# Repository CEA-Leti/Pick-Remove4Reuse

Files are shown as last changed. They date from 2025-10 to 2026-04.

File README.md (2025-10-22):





**Pick&Remove4Reuse**
---------------------
Système de récupération de composants électoniques automatisé basé sur une imprimante 3D open source Creality Ender3.

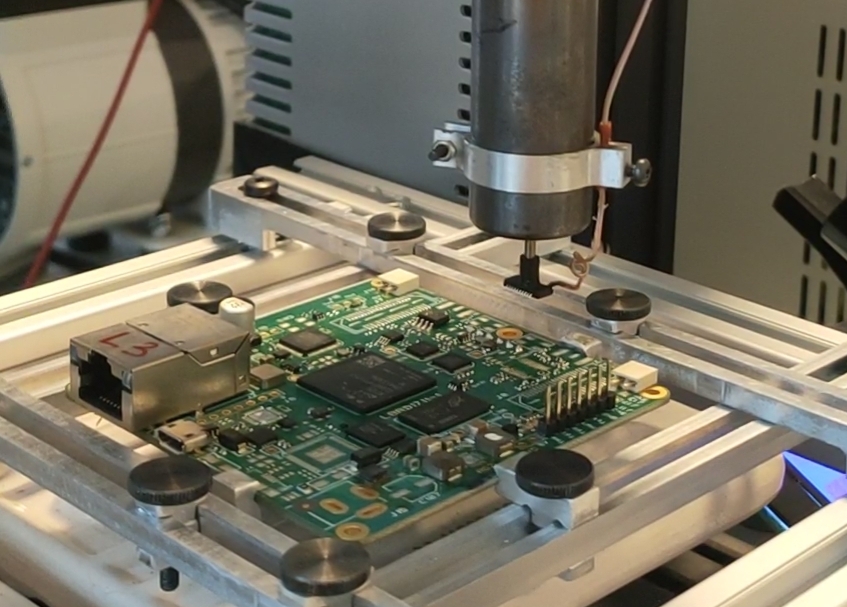
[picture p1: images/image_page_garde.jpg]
Récupération composants

## Introduction

Ce document a pour objectif de recenser le travail effectué lors de mon stage de fin d'étude qui avait pour objectif de concevoir un système automatisé de récupération de composants électroniques (ECs). Ce domument a également pour objectif d'assister tuote personne qui souhaiteraient reproduire ou reprendre ces travaux.
Mon rapport de stage, détaillant le travail effectué se trouve à l'adresse suivante :
> "doc/Rapport_PFE_Margaux_Anne_CEA_INSA.pdf"

Lors de mon stage, j'ai pu concevoir, fabriquer et tester une station de récupération automatisée de composants électroniques en vue de leur réemploi. Les résultats sont prometteurs. La station permet une récupération de composants CMS d'une taille pouvant varier en fonction de la taille de la buse. L'impact CO2 en termes d'énergie utilisée lors de la récupération s'est révélé inférieur à celui de la fabrication. Le temps nominal de récupération d'un composant électronique est de 1'30 et peut prendre jusqu'à 2'30.

## Prise en main rapide de la station une fois mise en place
*   Positionner la carte sur le support de carte. Il est nécessaire de dévisser uniquement les vis moletées se trouvant sur le bras de gauche et du haut. Attention, les bords de la carte doivent être alignés sur le support de carte. Le coin inférieur gauche de la carte une fois positionné doit correspondre au coin auquel les composants sont référencés dans le fichier de fabrication.
*   Vérifier que la ventouse du pistolet corresponde à la taille des ECs visé pour la récupération
*   Allumer la plaque IR pour préchauffe de la carte (15 min mini)
*   Brancher la carte Arduino et l'imprimante à l'ordinateur
*   Ouvrir le script python avec Spyder
> "src\Test_imprimante_positionement.py"
*   Utiliser python 3.10  (clique-droit sur la console>New console in environment>Custom: Python310)
*   Un fichier de config permet de configurer certains paramètres, on retrouve par exemple la hauteur de sécurité afin d'éviter que le pistolet ne percute des éléments de la structure ou de la carte. On retrouve également la hauteur delta permettant le chargement du ressort, permettant le désassemblage, cette hauteur peut être modulée en fonction du positionnement du capteur de fin de course et du chargement que l'on souhaite effectuer sur le ressort. Des valeurs prédéfinies sont rentrées, il est possible de les modifier au besoin.
> "src\config.ini"
*   Allumer l'imprimante et la station Hakko
*   Lancer le programme : ce dernier va commencer par initialiser l'imprimante. Il vous demandera ensuite de fournir un fichier Excel avec la position des ECs à récupérer. Un exemple de fichier se trouve au chemin ci-dessous. Une fois le fichier fournis, il vous sera demandé de référencer le premier composant à récupérer du fichier Excel. Pour ce faire, vous pouvez vous déplacer avec la molette de l'imprimante en suivant les instructions fournie par le programme. Une fois la position validée, la récupération débute. Des messages d'information sont visibles sur l'imprimante afin de vous tenir au courant sur l'avancée de la récupération.
> "src\composants_recup.xlsx"
*   Si vous voulez interrompre la récupération, faites 'ctrl C' dans la console. Il vous sera ensuite nécessaire de débrancher et de rebrancher la carte Arduino afin de relancer le programme sans erreurs.
*   Un mode d'emploi présente les explications ci-dessus en annexe du rapport de stage.

## État de l'art
Mon stage a débuté avec l'établissement d'un état de l'art qui recense un certain nombre d'articles scientifique sur les Déchets d'Équipements Électriques et Électroniques (DEEE), le recyclage des cartes et ECs, ainsi que sur la récupération des ECs en étayant également les perspectives en termes de conception alternative afin de faciliter la récupération, la réutilisation et le recyclage des systèmes électroniques.
Le document se trouve ici:
> "doc\Rapport_bibliographique_recuperation_EC.pdf"

## Choix des outils fonctionnels
L'essentiel des outils, dispositifs, achats effectuées au cours du stage sont recensées sur:

> "documentation\Materiel.xlsx"

## Conception
Après avoir fait les différents choix fonctionnels ainsi que choisi les briques fonctionnelles, la conception des différents éléments d'intégration a débuté.
Le fichier ci-dessous contient les différents sous-fichiers correspondants aux éléments de conception. 
> "solidworks"

La CAO du système général avec tous les éléments assemblés se trouve ici:
> "solidworks\support_carte_asm_g\asm_general_v3.SLDASM"

## Commande et mesure station Hakko
Afin de commander et d'avoir un retour de la station Hakko (commande du pistolet permettant le dessoudage et le désassemblage), il a été nécessaire d'ouvrir cette dernière.
Pour ce faire, il est nécessaire de dévisser les quatre vis fixant le cadre de la face avant de la station ainsi que les deux vis se trouvant sur la face arrière de cette dernière. Le cadre du bas tient alors encore en place grâce à un clip se trouvant sur la face du bas de la station accrochant le cadre avant et le carter de la station. Une fois déclipsée, il est  ainsi possible d'ouvrir la station. L'image ci-dessous illustre nos deux points d'intérêt. À savoir, le bouton permettant l'actionnement du cycle et le buzzer donnant des informations sur l'état du cycle.

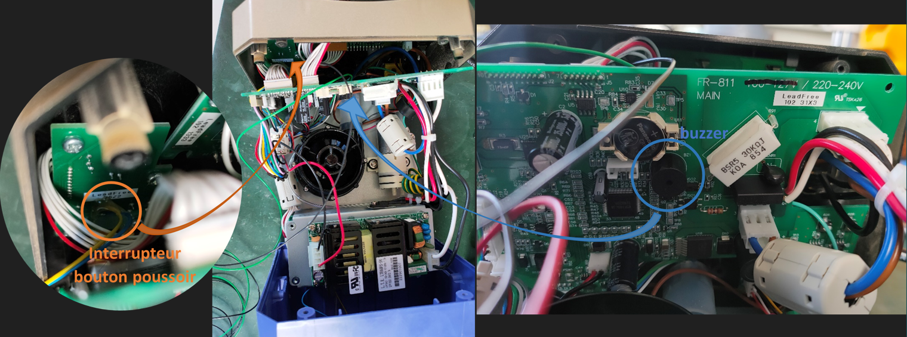
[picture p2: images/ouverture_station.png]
hghg Ouverture station Hakko


Il est alors nécessaire de souder des fils sur les bornes de l'interrupteur et celles du buzzer.

* Une fois ceci fait, les deux fils de l'interrupteur sont soudés sur un relai 5 V. L'objectif avec l'utilisation du relai est qu'il agisse comme un interrupteur commandé. Selon le signal de commande envoyé par la carte Arduino au relai, celui-ci effectue une connexion ou non entre les deux fils soudés aux bornes du bouton de la station, déclenchant/stoppant ou non le cycle de chauffe. Le fil soudé sur la commande du relai est branché sur un pin analog de la carte Arduino. Le second fil est lui relié au 5 V de l'Arduino. Une diode est également soudée entre les deux pins (commande/puissance) du relai.

* Les fils du buzzer sont eux fixés sur les pins de la carte Arduino. L'un des fils doit être relié à la masse, quant à l'autre à un pin digital (PWM) de l'Arduino. Lors du soudage des fils, celui devant être relié à la masse doit être vérifié. Pour cela, testez avec un multimètre quelle borne du buzzer y est connectée en vous aidant de la pile (se trouvant à côté de ce dernier sur la carte de la station) qui a elle-même une borne reliée à la masse.

## Intégration du capteur de fin de course:
Le capteur de fin de course est relié à la carte Arduino. Ce dernier possède 3 bornes. Une étude de la datasheet vous permettra de comprendre son fonctionnement. Dans la pratique, l'une des bornes sera reliée à l'alimentation de la carte (3,5 V par exemple) et l'autre à un pin digital de l'Arduino. Pour le bon fonctionnement, une résistance de pull down est également nécessaire pour cette même sortie.

## Commande - Script Python
En parallèle de la conception des différents éléments d'intégration, la commande du système a été conçue. Cette dernière est assurée par un script Python se trouvant ici :
> "src\PickRemove.py"

Ce dernier est associé à un fichier de configuration généré par un script Python permettant la modification de certains paramètres. Le réglage des paramètres est détaillé par la suite.

Afin que le script fonctionne, plusieurs choses sont nécessaires:

* Connexion en port série avec l'imprimante 3D : connecter l'imprimante et l'ordinateur en vérifiant que le numéro du COM série pré-rentré dans le fichier de configuration est le bon (vérifier à l'aide du gestionnaire de périphérique de votre ordinateur)

* Connexion à la carte Arduino permettant le contrôle du cycle de chauffe, la mesure de l'étape de ce dernier ainsi que l'état du capteur de fin de course. Connecter en port série la carte Arduino et l'ordinateur. Comme pour l'imprimante 3D, il est nécessaire de vérifier le numéro du COM série pré-rentré dans le fichier de configuration. 
Afin de configurer la carte Arduino lors de la première utilisation, un programme doit lui être transféré, permettant d'utiliser la librairie PyFirmata utilisée dans le script Python. Il est alors nécessaire de se rendre dans l'IDE Arduino 
`Fichier>Exemples>Firmata>StandarFirmata`

* Installer les différentes librairies :

    * Pour installer la bibliothèque pyFirmata il faut taper la commande suivante dans la console Python : `!pip install pyfirmata`

* Installation de la version `Python 3.10` afin d'utiliser la librairie pyFirmata. Une fois l'installation effectuer, il faudra dans la console Python générer une nouvelle console avec la version 3.10 (clique-droit sur la console>New console in environment>Custom: Python310).

## Réglage script Python
Les différents paramètre modifiable, pour le réglage du système de récupération, sont regroupés dans un fichier de configuration modifiable :

> "src\config.ini"

> "src\Creation_fichier_config.py"

Celui-ci permet de définir certains paramètre expliqué ci-dessous :
[DEFAULT]
* portImprimante = COM7
* portArduino = COM5
* baudrate = 115200 : vitesse de discussion entre le script Python et l'Arduino
* pin_finDeCourse = 7
* pin_buzzer = 2
* pin_relaiCycleChauffe = 4

[Constante]
* vitesse_deplacement = 3000 : définition de la vitesse de déplacement de l'imprimante

* pos_x_min_depose_ec = 96 : définition de la position en x du premier emplacement de dépose d'EC.
* pos_x_max_depose_ec = 229 : définition de la position en x du dernier emplacement de dépose d'EC.
* espacement_ec_depose_x = 19 : Espacement en x entre deux positions de dépose.
* pos_y_min_depose_ec = 35 : définition de la position en y du premier emplacement de dépose d'EC.
* pos_y_max_depose_ec = 38.8 : définition de la position en y du dernier emplacement de dépose d'EC.
* espacement_ec_depose_y = 0.4 : Espacement en y entre deux positions de dépose.
* hauteur_secu_z = 35 : hauteur de sécurité afin de ne pas percuter des éléments avec le pistolet lors de ses déplacements en x et y.
* delta_z_posDesassemblage = 4 : distance delta nécessaire pour venir charger le ressort lors du désassemblage.

## Initialisation station Hakko
Initialisation du cycle de chauffe dans la station Hakko. Le cycle de chauffe prédéfini à charger sur la station se trouve ici:
>"src\Hakko\cycle_chauffe_hakko.csv"

Trois options s'offrent à vous :
* Réglage manuel directement sur la station
* Import du cycle via une clé USB
* Import du cycle via le port série de l'ordinateur (nécessite l'installation d'un pilote sur l'ordinateur). La démarche à suivre est décrite dans le manuel d'utilisation de la station.

La courbe de température à suivre est détaillée dans le fichier OneNote ci-dessous :
>"doc\Température dessoudage.one"

## Modification Imprimante 3D
*   **Modification des branchements de la carte**:
La carte de l'imprimante 3D se trouvant sous le plateau de cette dernière (cf image ci-dessous) permet de commander l'imprimante en position avec la commande de trois moteurs pas à pas (un pour chaque axe). Afin de faire le 0 de l'imprimante, la présence de capteurs de fin de course est également nécessaire. Nous retrouvons aussi un ventilateur permettant de prévenir la carte d'une potentielle surchauffe. La carte est par ailleurs alimentée, nous retrouvons ainsi deux fils branchés sur un bornier dans le but d'assurer cette fonction.
Outre ces fonctions, on retrouve aussi des éléments propres à l'impression 3D : alimentation de la chauffe de la buse (bornier 3 sur l'image ci-dessous) et du plateau (2), ventilateur lié à la buse (1), thermistance afin de mesurer la température de la buse et du plateau et permettre leur régulation respective. Ces derniers éléments ne nous sont plus nécessaires, ainsi, nous pouvons les enlever pour ne garder que l'utile de l'imprimante. Attention, il n'est néanmoins pas possible de retirer les thermistances. En effet, une fois débranchée, la température mesurée est erronée, ce qui engendre une erreur de l'imprimante. Ainsi, nous pouvons uniquement retirer les éléments branchés aux trois borniers latéraux gauches (1,2 et 3) ainsi que la commande du moteur d'approvisionnement en filament. Le premier bornier, initialement prévu pour l'alimentation du ventilateur associé à la buse d'impression, fournit une tension de 24V en continu. Ainsi, nous pouvons nous en servir afin de brancher un régulateur en température si besoin est de réguler la plaque IR. Dans mon cas d'étude, la plaque IR était alimentée à 60V, avec un générateur de puissance, ce qui ne permettait pas d'atteindre une température de préchauffe de la carte supérieure à 130°C. Ainsi, il n'a finalement pas été nécessaire de la réguler en température, étant donné que le seuil de préchauffe à ne pas dépasser est beaucoup plus haut (150-200°C). S'il vous est nécessaire de réguler en température la plaque, il est alors possible d'utiliser un régulateur de température, en fonction de la tension de commande max de l'outil en question, vous aurez peut-être besoin de réguler la tension sortant du bornier avec un régulateur 24V --> 5V par exemple. La puissance peut elle provenir directement du générateur 60V dans le cas où votre régulateur est isolé entre la commande et la puissance.
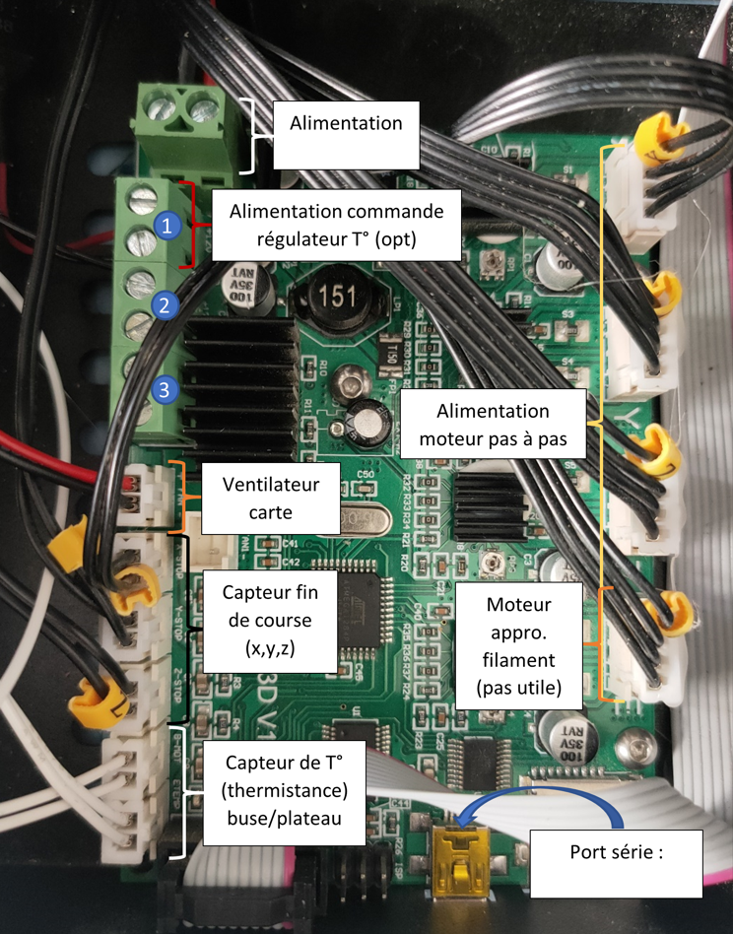
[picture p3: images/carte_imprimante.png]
hghg Carte imprimante 3D


*   **Modification sur la structure de l'imprimante:**
    * Afin de limiter le poids se trouvant sur la structure de l'imprimante se déplaçant selon z, vous pouvez démonter le moteur pas à pas initialement prévu pour l'approvisionnement en filament.
    
    * Afin de limiter la course de l'imprimante selon z et ainsi empêcher la collision du pistolet avec la structure de l'imprimante, il est conseiller de déplacer le capteur de fin de course de l'axe z vers le haut (il est possible qu'il soit nécessaire de rallonger les fils reliant ce dernier à la carte de l'imprimante présenté en amont)

    * La tête d'impression tout comme la plaque chauffante doivent être démonté. Le pistolet sera intégré directement sur le support de la tête d'impression (comme illustré dans la CAO générale du système introduite en amont). Le support de carte sera lui monté directement sur le support de la plaque chauffante, tout comme le support de la plaque IR.

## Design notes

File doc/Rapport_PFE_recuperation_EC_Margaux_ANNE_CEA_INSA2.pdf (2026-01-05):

Margaux ANNE
Année universitaire 2024–2025

### Spécialité Mécatronique - Parcours P4 Master Imagerie, Robotique et Ingénierie pour le Vivant (IRIV)

Projet de fin d’étude MIQ5 - Mémoire de stage de Master 2

# Développement d’un système automatisé de récupération de composants électroniques en vue de leur réemploi

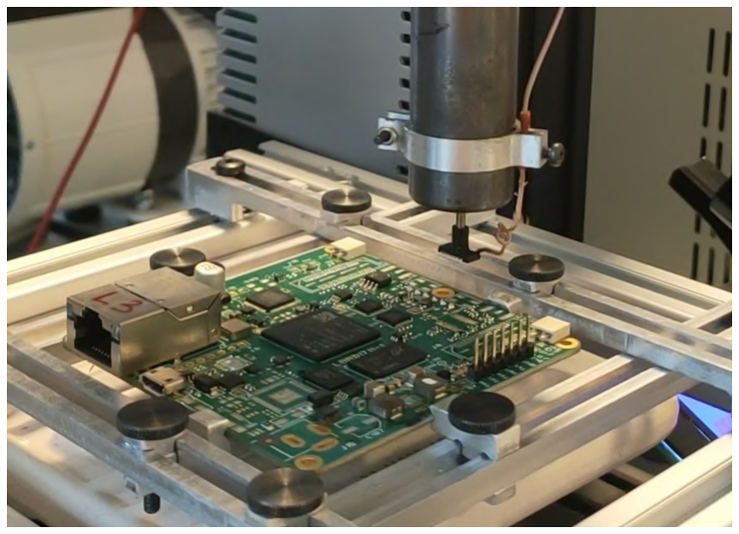
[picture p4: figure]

Organisme d’accueil :
CEA Grenoble
Encadrant : Sébastien BRULAIS
Adresse : 17 Av. des Martyrs, 38000 Grenoble Courriel : sebastien.brulais@cea.fr

Dates du stage : du 03/03/2025 au 21/03/2025 et du 07/04/2025 au 03/09/2025

## Résumés

### Résumé

Face au défi croissant posé par les déchets d’équipements électriques et électroniques (DEEE), un système automatisé a été développé pour récupérer des composants électroniques (EC) destinés à une réutilisation directe dans une logique de « seconde vie ». Ce projet répond à l’urgence d’agir contre l’augmentation des DEEE, qui représentent un risque majeur pour l’environnement et la santé. Avec l’accélération des avancées technologiques et la réduction de la durée de vie des appareils, la quantité mondiale de DEEE devrait atteindre 82 millions de tonnes d’ici 2030 [7]. Les méthodes classiques de gestion, comme la mise en décharge ou l’incinération, ne sont plus viables et engendrent des impacts environnementaux négatifs. Il devient donc essentiel de développer des solutions innovantes de recyclage et de réutilisation des ECs dans une logique d’économie circulaire [34]. Alors que certaines initiatives visent à extraire en masse des matériaux rares via des procédés chimiques (Ta, Ti, Ag, Au, . . .) [3], l’approche proposée cherche à récupérer des ECs à forte valeur ajoutée pour une réutilisation directe.
Un état de l’art a permis d’identifier les ECs présentant un fort intérêt économique et environnemental, ainsi que les méthodes adaptées à leur récupération sécurisée. Sur cette base, un outil de type « pick and remove » a été conçu. Sa structure repose sur le châssis d’une imprimante 3D Ender3 modifiée. Le préchauffage est assuré par un chauffage infrarouge (jusqu’à 150 °C), tandis qu’un pistolet muni d’une buse à air chaud (jusqu’à 260 °C) et d’un système d’aspiration assure le dessoudage localisé et le retrait des composants. Un script Python pilote la tête de l’imprimante, sur laquelle le pistolet est fixé, afin d’automatiser la récupération sur de petites séries de cartes.
Les premiers essais ont confirmé la faisabilité et l’efficacité du système, tout en apportant une première évaluation de ses bénéfices potentiels, tant économiques qu’environnementaux.

### Abstract

In response to the increasing challenge of electronic waste (e-waste), an automated system has been developed for disassembling electronic boards and recovering components for direct reuse in a "second life" approach. The motivation behind this project stems from the urgent need to address growing issue of electronic waste, which poses substantial environmental and health risks. With technological advancements and shorter device lifespans, global e-waste is projected to reach 82 million tons by 2030 [7]. Traditional waste management methods, such as landfilling and incineration, are no longer sustainable and harmful to the environment. Innovative solutions for recycling and reusing electronic components (ECs) are essential for promoting a circular economy and reducing the environmental impact of e-waste [34]. While some initiatives focus on mass recovering of ECs to recycle rare materials through chemical processes (Ta, Ti, Ag, Au,. . .) [3], the proposed approach aims to recover high-value ECs for direct reuse in second-life applications.
A literature review has firstly been performed to identify components with high economic and environmental relevance and associated methods for their safe recovery. Based on this review, a "pick and remove" tool tailored to the needs for automation and component preservation has been developed. The structural framework of this tool is based on a widely used Ender3 3D printer body. A dedicated PCB card holder was created to securely position the PCB during disassembly. Pre-heating is achieved with an IR heater (up to 150 °C), and a hot air nozzle has been integrated for final heating (up to 225°C), ensuring precise and localized desoldering. A Python script has been developed to control the 3D printer body and the hot air nozzle to automate the recovery of components from small series of PCBs.
Preliminary tests have demonstrated the system’s feasibility and effectiveness in automatically recovering electronic components. These tests also enabled an evaluation of the potential economic and environmental benefits of this innovative approach.

## Remerciement

Je tiens tout d’abord à remercier le CEA de Grenoble qui m’a accueillie en son sein pendant mes six mois de stage.
Plus particulièrement, je remercie mes tuteurs, Sébastien BRULAIS et Tristan CAROFF, pour leur expertise et leurs conseils tout au long de ce projet. Leur soutien et leur confiance m’ont permis d’effectuer un stage formateur qui m’a fait gagner en maturité et en expérience. Ce stage a été pour moi une expérience professionnelle très enrichissante à travers laquelle j’ai pu fournir un travail dont je suis contente.
Je remercie également l’ensemble des personnes du laboratoire LAIC pour leurs conseils, mais également pour leur bonne humeur et leurs discussions vivantes qui ont rendu mon stage épanouissant sur le plan humain. Et je remercie avec une attention particulière Vincent ELHORGA pour son aide lors de la fabrication de mes pièces.
Outre le laboratoire LAIC, je remercie les différents acteurs du groupe éco-innovation pour leurs conseils, leur gentillesse et leur personnalité vivante qui m’ont beaucoup apporté.
Je souhaite aussi remercier mon école, l’INSA de Strasbourg, ainsi que Télécom Physique Strasbourg qui m’ont permis d’effectuer ce stage dans le cadre de ma formation d’ingénieur en mécatronique. Je remercie tout particulièrement mon tuteur de stage Pierre RENAUD pour son suivi et ses remarques avisées. Finalement, je remercie toutes les personnes qui m’ont épaulée et accompagnée pendant toutes mes années de formation, participant ainsi à la réussite de mon stage de fin d’études.

## Table des matières

Résumés | 1
Remerciement | 2
Listes et index divers | 5
Introduction | 7
1 But du travail | 8
2 Contexte | 9
3 Etat de l’art | 12
4 Description des méthodes utilisées | 25
5 Description des réalisations | 29

6 Résultats obtenus | 39
Conclusion | 43
Références | 46
Annexes | 47

## Listes et index divers Glossaire

CAPEX Investissement initial. 17
CRMs Matières premières critiques. 14, 23
DEEE Déchets d’Equipements Electriques et Electroniques. 7, 9, 12
EC Composants Electroniques. 7–9
G-code Consiste en une série de commande et de paramètre indiquant les déplacements que la machine doit effectuer. 38
IRIV Imagerie, Robotique, Ingénierie pour le Vivant. 7
OPEX Coût opérationnel. 17
PCB circuits imprimés. 13–16, 21, 23, 27
SMD dispositifs montés en surface. 19, 20
THD dispositifs traversant. 19, 20
WPCB déchets issus des cartes de circuits imprimés. 13, 14, 19, 22, 24, 43

## Table des figures

1 | Implantation du CEA | 10
2 | Organigramme DSYS | 11
3 | Comparaison entre l’évolution technologique (a) et scientifique (b) des procédés de valorisation
| des cartes électroniques en fin de vie | 13
4 | Taux de défaillance expérimental qui peut être subdivisé en trois zones : mortalité infantile (1),
| échec aléatoire (2) et vieillissement (3) | 15
5 | Courbe de température brasage ECs | 18
6 | Impact température brasage ECs | 19
7 | Les deux types de dispositifs pour les ECs : (A) SMD et (B) THD | 20
8 | Diagramme de GANTT | 26
9 | Courbe de température dessoudage | 27
10 Schéma fonctionnel | 28
11 Imprimante Ender 3 | 29
12 Support carte | 30
13 Pièce support carte | 30
14 Support carte conçu et fabriqué | 30
15 Support plaque IR | 31
16 Support plaque IR fabriqué | 31
17 Système de récupération non contraint en hauteur d’EC | 32
18 Fonctionnement du désassemblage | 32
19 Éléments de liaison entre le patin et le pistolet | 33
20 Éléments d’intégration du pistolet | 34
21 Intégration du pistolet | 35
22 Répartition température | 35
23 Pièces de maintien pour la bague | 36
24 Bague pour intégration du thermocouple | 36
25 Système de récupération d’EC | 37
26 Plan synoptique | 37

27 Flowchart de la commande | 38
28 Comparaison de la distance pistolet–EC sur les trois configurations | 40
29 Comparaison de l’impact du flux utilisé sur la température mesuré | 41
30 Dépose d’un EC | 42
31 Axes de recherche LAIC | 47
32 Flyer présentation CEA Tech | 48
33 Etat de l’art | 50
34 Assembly solder profile | 73
35 Critère de réutilisation ECs | 75
37 Ouverture station | 77

## Liste des tableaux

1 | Comparaison des méthodes de dessoudage | 17
2 | Comparatif des méthodes de dessoudage pour une station automatisée | 19
3 | Résumé des techniques de désassemblage | 20
4 | Score EI pour différents produits électroniques | 23
5 | Valeurs EI-99 de matériaux utilisés en électronique | 23
6 | Comparatif des ECs selon leur composition, impact environnemental et économique | 24
7 | Cahier des charges fonctionnel | 27

## Introduction

De nos jours, la plupart des Déchets d’Equipements Electriques et Electroniques (DEEE) ne sont pas traités convenablement, ce qui engendre une perte de métaux rares/précieux et un rejet de matière toxiques directement dans notre environnement. Outre les répercussions environnementales, ces rejets impactent également notre santé. Dans le meilleur des cas, les DEEE sont traités avec précaution vis-à-vis de leur dangerosité, mais cela se limite au recyclage sans exploitation du plein potentiel de ces déchets. En effet, lorsque l’on parle de recyclage, nous entendons un broyage de cartes électroniques dans l’optique d’une extraction de certains matériaux. Par suite, les Composants Electroniques (EC)s sont détruits afin de ne récupérer qu’une partie de leur composition. Pourtant, ces derniers n’auraient atteint que 5% de leur durée de vie [2]. Ainsi, la récupération des EC pourrait nous ouvrir une porte vers la revalorisation. La valeur ajoutée de ces derniers serait alors conservée et leur durée de vie augmentée.
Dans le cadre du développement de son activité R&D autour de l’éco-innovation et l’économie circulaire, le laboratoire LAIC du Département Systèmes du CEA-LETI à Grenoble propose un stage ayant comme objectif le développement d’un système automatisé de récupération d’ECs en vue de leur réemploi.
Ainsi, afin de finalisé ma formation d’ingénieur en mécatronique ainsi que mon master en Imagerie, Robotique, Ingénierie pour le Vivant (IRIV) j’ai eu la possibilité de réaliser ce stage dans le cadre de mon Projet de Fin d’Étude (PFE).
À travers ce stage, l’établissement d’un état de l’art a permis de définir les différentes thématiques liées à la récupération des ECs, notamment l’identification et le tri, le dessoudage, le désassemblage et les tests. Cette étude a par ailleurs mis en évidence les problématiques associées, telles que l’endommagement des ECs et leur fiabilité.
Une fois cette première phase accomplie, un cahier des charges associé à une analyse fonctionnelle simplifiée ont étés construits et un choix de solution pour le système a été fait. S’en est suivi une phase de conception et de fabrication des différentes briques fonctionnelle. Après une intégration des différents éléments du système, un ensemble de tests fonctionnels a pu être réalisé, et par la suite quelques améliorations ont encore pu être apportées au système.

## 1 But du travail

Les objectifs du travail étaient multiples, nous verrons dans cette section les différentes thématiques abordées ainsi que leurs objectifs. Étant donné qu’il s’agissait d’une nouvelle thématique pour le laboratoire, j’en ai assuré l’étude et l’exécution de manière autonome, depuis la phase initiale.

### 1.1 Nature du travail

Comme énoncé précédemment, l’objectif principal du stage est la réalisation d’un système automatisé de récupération d’ECs en vue de leur remploi. Dans un même temps, les limites et les points bloquants que peut représenter cette thématique ont été étudiés. Nous distinguons alors au sein de l’objectif principal plusieurs thématiques : la récupération, l’automatisation et le réemploi.
Au cours du stage, la nature du travail a pris plusieurs formes. Dans un premier temps, elle a consisté à la réalisation d’un état de l’art. L’objectif est alors de prendre pleinement connaissance du problème grandissant que représentent les DEEE. Par cette étude bibliographique, des articles faisant part de propositions de solutions pour le recyclage au sens large ont pu être étudiés. Des propositions visant à simplifier le recyclage, la réutilisation ou encore la récupération m’ont donné un nouveau regard sur nos méthodes de conception. En somme, cette étude bibliographique a permis de prendre connaissance de l’étendue des domaines d’action, mais aussi du manque d’études et de données sur le sujet du recyclage des ECs.
Suite à cet état de l’art, une analyse fonctionnelle simplifiée couplée à la formalisation d’un cahier des charges a permis d’identifier les fonctions et sous fonctions clés du système de récupération d’ECs ainsi que les points de vigilance/contraintes associés.
L’étude d’une solution a ensuite été menée en s’inspirant des idées partagées dans les articles du domaine de la récupération d’ECs. Une simplification du problème et du champ d’application ont également dû être faits afin d’aboutir à un prototype opérationnel pendant la durée du stage.
Une fois cette phase aboutie, la nature du travail a pris une nouvelle forme avec le choix de solutions pour les différentes briques fonctionnelle dégagé en amont. Des choix matériels ont alors était fait. L’intégration de ces derniers a également mener à la conception et la fabrication de différentes pièces. En ce qui concerne l’automatisation, un script python a été développée afin de réaliser la commande de l’ensemble du système de récupération des ECs.
Cette phase a mené à la réalisation d’une première version du système de récupération. Une phase de test et d’ajustement a alors débuté. De nombreuses solutions ont été étudiées et mises en place pour permettre les ajustements nécessaires au bon fonctionnement du prototype.
Une fois le système suffisamment abouti, des tests de répétabilité et d’endommagements des ECs ont été conduits.
En somme, la nature du travail a pris différentes formes au cours du stage dans l’optique de rechercher une solution en phase avec les possibilités du laboratoire ainsi que mes compétences et le temps alloué tout en satisfaisant l’objectif de la récupération automatisée et facilement implémentable.

### 1.2 Insertion dans un contexte plus large

Au sein du laboratoire, le sujet est nouveau, mais tend à prendre de l’ampleur. À l’échelle du service, de nombreuses personnes sont intriguées par le sujet et seraient intéressées par les possibilités offertes par la récupération et le réemploi d’ECs.
Le stage ayant pour objectif la fabrication et le prototypage d’un dispositif intégrant les contraintes de soutenabilité environnementale, il s’inscrit dans le groupe éco-innovation qui rassemble plusieurs sujets à l’échelle du centre de Grenoble. Cette ouverture à des domaines étendus a permis la mise en relation avec plusieurs acteurs. Ainsi, j’ai pu grâce à ce cercle rentrer en contact avec des chercheurs de l’INSA de Rennes ou encore un doctorant de 2ème année au CEA de Saclay. Une entrevue avec ces différents acteurs a permis le partage d’informations sur le sujet ainsi que la discussion de nos objectifs au sein des différents organismes afin d’identifier la possibilité de travailler ensemble et d’étendre davantage le sujet du recyclage et du réemploi des ECs. Le partage des difficultés rencontrées a également permis de renforcer les observations que nous avions eues chacun de notre côté.
Dans une autre dynamique, la réalisation d’un abstract sur le sujet pour participer à une conférence a été soumis. L’objectif sera alors de partager mes avancées, les connaissances acquises, de sensibiliser ainsi que de créer un réseau avec d’autres personnes intéressées ou travaillant aussi sur le sujet.

### 1.3 La dimension «recherche»

Au sein du stage, la dimension recherche a pris plusieurs formes.
Dans un premier temps, l’établissement d’un état de l’art a permis de fournir une compréhension exhaustive des travaux antérieurs dans le domaine de la récupération des ECs, mais aussi au sens large du recyclage des DEEEs. Cette rédaction a ainsi permis de fournir des informations à différents acteurs dans ce domaine afin d’avoir du recul, de prendre conscience de l’ampleur du sujet et de la variété des thèmes pouvant être étudiés. L’identification des lacunes dans le monde de la recherche dans ce domaine a également permis de se rendre compte de l’importance d’étudier ce sujet qui, à juste titre, a éveillé notre intérêt au vu des chiffres alarmants que représentent les DEEEs, mais aussi au vu de la problématique lié aux matériaux critiques (matières premières qui sont les plus importantes sur le plan économique et qui présentent un risque élevé de pénurie d’approvisionnement).
Ainsi, l’un des objectifs du stage était de mettre le pied à l’étrier sur ce sujet de recherche encore peu étudié. L’état de l’art a permis d’établir une base afin de développer la recherche autour du sujet. En effet, l’objectif était de pouvoir identifier des axes de recherche pour la suite du projet ainsi que les points durs à anticiper. En somme, contribuer à l’aspect recherche du laboratoire en développant les possibilités autour de ce sujet de revalorisation de nos DEEEs. La construction d’une roadmap, pour le laboratoire LAIC, a ainsi commencé dans ce sens.
Par ailleurs, la mise en place d’un système automatisé de récupération d’ECs représente en soit un outil d’investigation pour la recherche. Le laboratoire souhaite par exemple développer la recherche autour de la thématique du test des ECs afin d’estimer leur état, leur valeur résiduelle et leur fiabilité. Par suite, l’accès à la station de récupération permettra de faciliter l’accès à des ECs de seconde main.
La mise en relation avec différentes personnes concernant mon sujet a également permis de prendre conscience du manquement de données sur cette thématique et de l’intérêt suscité. Dans cette optique, un des objectifs secondaire du stage serait de rendre le projet open source afin de donner accès à la récupération dans le but d’ouvrir de nouvelles portes dans ce domaine.
L’évaluation de l’impact environnemental (via une ACV) de la récupération directe des ECs représente par ailleurs une thématique importante du sujet. Par ce stage, nous souhaitons avoir une première idée de l’impact de la récupération, dans l’optique de déceler des points d’attention liés au procédé et ainsi nous guider dans son optimisation.

## 2 Contexte

À présent que le but du travail a été introduit, nous allons pouvoir nous concentrer sur le contexte du stage. Ainsi, nous allons commencer par une présentation générale du CEA pour finalement contextualiser plus précisément le stage au sein du laboratoire dans lequel j’ai travaillé.

### 2.1 Contexte de l’entreprise

### 2.1.1 Le CEA

Le CEA, Commissariat à l’énergie atomique et aux énergies alternatives, est un organisme de recherche classé en établissement public à caractère industriel et commercial (EPIC). Créé en 1945 sous la demande du général de Gaulle, le CEA naît avec comme vocation de devenir un organisme de recherche consacré à l’énergie atomique. Implanté sur neuf centres (figure 1) répartis dans toute la France, il développe de nombreux partenariats avec les autres organismes de recherche, les collectivités locales et les universités. Ainsi, le CEA dénombre plus de 22000 collaborateurs et plus de 700 partenaires industriels. 1er organisme de recherche français déposant de brevets en Europe, le CEA comptabilise un budget annuel de 6,4 milliards d’euros en apportant des solutions concrètes dans quatre domaines principaux :
— les énergies bas-carbone (nucléaire et renouvelables)
— le numérique,
— les technologies pour la médecine du futur,
— la défense et la sécurité.

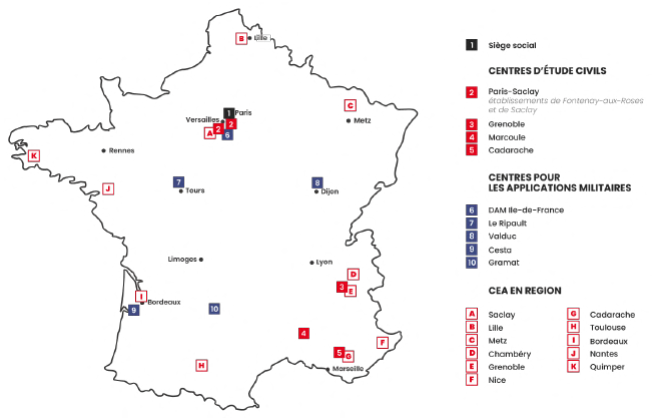
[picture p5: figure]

Figure 1 – Implantation du CEA

Pour mener à bien ses missions, le CEA s’appuie sur quatre directions dites opérationnelles : — Direction des énergies
— Direction des applications militaires
— Direction de la recherche technologique
— Direction de la recherche fondamentale
Dans le cadre de mon stage, je travaille au sein de la direction de la recherche technologique, aussi appelée CEA TECH. Cette dernière se concentre sur la recherche technologique, c’est-à-dire la « production de technologies » et leur diffusion à l’industrie. CEA Tech dispose d’une offre très large de technologies génériques issues de ses trois instituts Leti, List et Liten tous trois implémentés sur le centre de Grenoble. On retrouve en annexe 32 un flyer de présentation de cette direction.

### 2.1.2 Le centre CEA de Grenoble

Nous arrivons ainsi à l’échelle du CEA de Grenoble comprenant le Leti, List, Liten déjà introduit ainsi que Irig se consacrant à la recherche fondamentale. Au cours de mon stage, j’ai évolué au sein du Leti.
Le Leti, pionnier dans les domaines des micros et nano-technologies, est un institut de recherche technologique. Avec 2 000 ingénieurs chercheurs et ses 11 000 m2 de salles blanches, le Leti s’intéresse à l’énergie bas-carbone, au numérique, aux technologies pour la médecine du futur, la défense et la sécurité.
Le Leti est divisé en plusieurs départements, on retrouve entre autres le DSYS, Département SYStèmes, dans lequel se situe le service SSCE, Service Systèmes de Capteurs électroniques pour l’Energie. C’est au sein de ce dernier que se trouve finalement mon laboratoire, le LAIC, Laboratoire Autonomie et Intégration des Capteurs. L’organigramme ci-dessous, regroupe ces différentes structures.

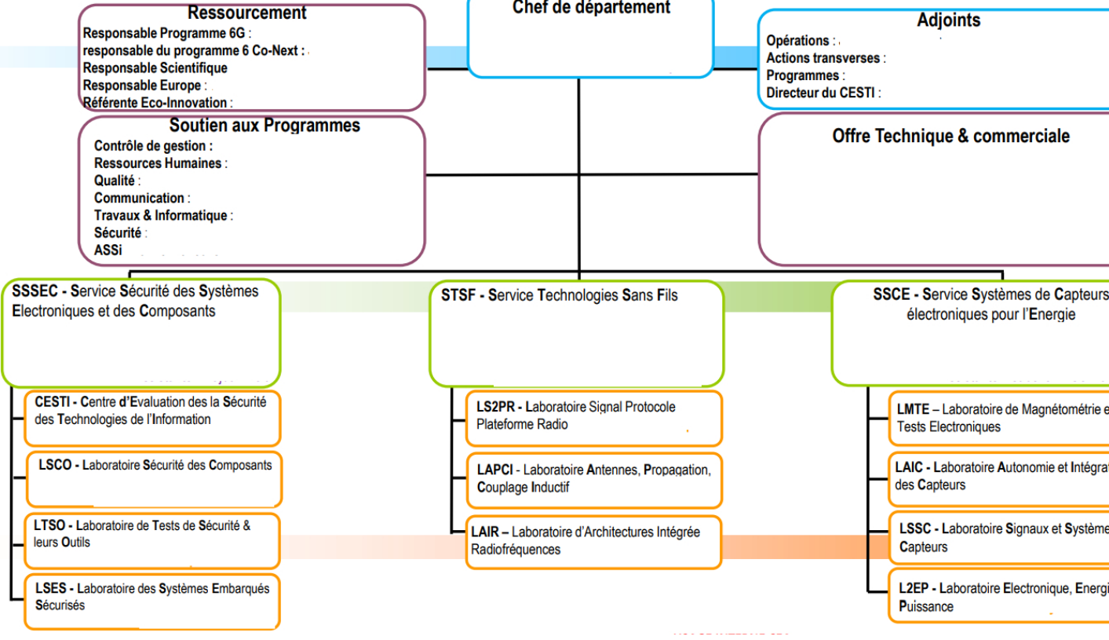
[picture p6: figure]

Figure 2 – Organigramme DSYS

Le LAIC se concentre sur plusieurs axes de recherche que l’on retrouve en annexe 31. Avec le début du stage, un nouvel axe est en train d’émerger :"reuse and sustanability". L’objectif est de développer au sein du laboratoire une nouvelle thématique autour de la récupération des ECs.

### 2.2 Contexte du stage

### 2.2.1 LAIC

Au sein du laboratoire LAIC mon supérieur hiérarchique est le chef du laboratoire, Sébastien BOISSEAU. Mes deux tuteurs, Sébastien BRULAIS et Tristan CAROFF sont tous deux ingénieurs chercheurs. Sébastien est spécialisé en électronique et Tristan est chef de projets. Tous deux ont commencé à voir du potentiel dans la récupération des ECs durant la crise covid. Durant cette période, l’approvisionnement de certains ECs était complexe. Délai à rallonge, rupture de stock, etc... En somme, l’accès aux ECs était devenu limitant, ce qui empêchait l’avancement de certains projets. La solution qu’ils ont trouvée à ce moment-là a été de récupérer les ECs dont ils avaient besoin parmi les cartes obsolètes qu’ils n’utilisaient plus, mais qui contenaient ce dont ils avaient besoin. Pour cela, ils se sont servis d’une station de récupération manuelle, Ersa [6]. Au-delà de l’aspect pratique de cette démarche, l’impact environnemental était réduit sans pour autant impacter le fonctionnement des prototypes fabriqués. Cette prise de conscience associée à la promotion du thème de l’éco-innovation au sein du Leti qui pousse au développement de démarches au tour de l’innovation responsable à permis de faire émerger l’idée et de proposer mon stage, "Développement d’un système automatisé de récupération d’EC en vue de leur réemploi". Ainsi, le sujet est tout nouveau au sein du laboratoire et tend à se développer, comme nous le verrons par la suite.

### 2.2.2 Groupe éco-innovation

Le groupe éco-innovation, interne au cea Grenoble, a pour objectif de trouver des solutions aux nombreux défis environnementaux auxquels l’industrie électronique est confrontée actuellement. L’institut propose une infrastructure complète et des méthodes qui couvrent :
— Le développement et la mise en œuvre d’analyses du cycle de vie (ACV), y compris la production de données ACV pertinentes pour mesurer les impacts environnementaux
— Les essais de validation de solutions éco-innovantes, dans un environnement R&D à l’état de l’art, de type production, avec des impacts mesurés, liés à la salle blanche, aux processus et aux équipements — Le développement de technologies et de systèmes de bout en bout pour répondre à des critères environnementaux spécifiques pour des cas d’application identifiés.

Mon stage s’inscrivant dans cette dynamique, j’ai été en relation avec ce groupe tout au long de mon stage. L’échange a pris la forme de réunion mensuelle afin que chaque stagiaire, rattaché au groupe, présente ses avancées afin de discuter des possibles points bloquants. Dans mon cas, il m’a également permis de rentrer dans un cercle plus large et de rentrer en contact avec des personnes intéressées par le sujet en dehors de mon laboratoire. Au courant du mois de juillet, nous avons aussi eu l’occasion de présenter nos stages lors d’une journée des stages où toute personne du LETI était invitée. Ainsi, j’ai également eu la possibilité de sensibiliser les auditeurs à cette thématique et aux possibilités envisagées.

### 2.2.3 Cadre du stage

Avec mon appartenance au laboratoire et au groupe éco-innovation, j’ai pu respectivement évoluer dans un cadre plutôt technique orienté vers la recherche, mais aussi dans un cadre relationnel d’échange. Au sein du laboratoire, j’ai pu rentrer en contact avec des personnes ayant diverses compétences. Ainsi, leur expertise m’a accompagné au long du stage afin de discuter au besoin sur des choix de solutions que j’avais faits et me permettre de gagner en compétences. D’un point de vue organisationnel, nous avions convenu avec mes deux tuteurs d’un rendez-vous hebdomadaire qui me permettait d’exposer mes avancées, mes choix techniques ou encore mes objectifs à venir. Ces moments de discussion m’ont permis de structurer mon avancée et de mettre à jour un planning sur l’ensemble de la durée du stage.

## 3 Etat de l’art

Au cours du stage, une étude bibliographique a été menée dans l’optique de fournir un état de l’art complet sur le sujet de la récupération des ECs. À travers cette partie du rapport, nous allons retracer les éléments-phare de ce dernier. La version de l’état de l’art complet se retrouve en annexe 33. Dans cette version condensée, nous essaierons d’aller à l’essentiel afin de synthétiser les tenants et aboutissants de l’étude. Nous commencerons par poser le contexte global pour mieux comprendre la place qu’occupent les DEEE dans le monde. Ensuite, nous nous intéresserons aux problématiques que posent ces déchets : comment ils sont traités aujourd’hui, quelles alternatives ont été testées, et où se situe notre travail là-dedans. Cette partie nous mènera naturellement aux contraintes que soulève la récupération d’ECs.
Nous passerons ensuite aux méthodes de récupération existantes et aux étapes qu’elles demandent. Nous verrons qu’elles dépendent fortement du type d’ECs visés. C’est pour cela qu’une nouvelle partie sera dédiée à l’analyse des ECs intéressants à récupérer. Nous discuterons alors des impacts de la récupération : économiques, sociétaux et environnementaux, de manière générale au niveau des DEEE, mais aussi de façon plus ciblée au niveau des ECs.
À partir de là, nous pourrons aborder les applications concrètes déjà mises en place dans le contexte de la récupération d’ECs. Ce qui nous mènera finalement à la conclusion de cet état de l’art avec les perspectives offertes par cette étude et les manques encore présents dans la recherche actuelle.

### 3.1 Contexte : l’impact mondial des DEEE

### 3.1.1 Les DEEE : proportion

Selon le quatrième Global E-waste Monitor (GEM) publié par l’ONU [7], la production mondiale de DEEE en 2022, a généré un volume atteignant les 62 millions de tonnes (Mt), soit une augmentation de 82% par rapport à 2010. Les projections indiquent une croissance de 32% supplémentaire d’ici 2030, pour atteindre environ 82 Mt. Parmis ces déchets, seuls 22,3% ont été correctement collectés et recyclés, ce qui correspond à une valeur estimée de 62 milliards de dollars de ressources récupérables non exploitées. Cette situation accroît également les risques de pollution pour les populations à l’échelle mondiale.
Parmi eux, on retrouve de nombreux ECs rares, coûteux ou contenant des matières toxiques. La plupart sont encore fonctionnels et n’ont été utilisés qu’une partie de leur durée de vie. Selon une étude [27], une grande partie d’entre eux n’ont atteint qu’approximativement 5 % de leur durée de vie prévue [27].
Ce domaine possède donc un important potentiel d’évolution. L’accès à certains métaux rares ou encore les crises (crises sanitaires, économiques ou de guerre) impactent directement notre capacité à nous procurer des ECs. Pouvoir les récupérer à partir de nos DEEE quotidiens pourrait donc représenter un atout économique, en plus d’un bénéfice environnemental, d’autant plus que l’urgence écologique pourrait, dans les années à venir, engendrer des restrictions qui rendraient cette démarche encore plus attractive.

### 3.1.2 La gestion des DEEE dans les différentes régions du monde

La surproduction de DEEE est devenue un problème urgent dans le monde entier. Ces derniers contiennent un grand nombre d’ECs qui peuvent avoir des effets nocifs sur l’environnement et les êtres humains. D’autre part, la manipulation sans précaution ainsi qu’un recyclage imprudent des DEEEs peuvent faire de ces derniers un problème de santé publique et environnemental à l’échelle mondiale. Ainsi, les pays à travers le monde se préoccupent de plus en plus de ce sujet, d’autant plus qu’en raison de leurs propriétés physiques, les DEEE sont parfaitement adaptés au recyclage et peuvent apporter des ressources rares lorsqu’ils sont recyclés. L’article [34] présente la place du recyclage de DEEE dans le monde. On apprend alors que dans les pays en développement, le recyclage reste majoritairement informel, avec des procédés manuels, peu sûrs et polluants. Le manque de normes techniques, d’automatisation, et de tri efficace empêche la réutilisation optimale des ECs précieux. Par contraste, les pays développés utilisent des technologies avancées de tri et de démontage, mais ces techniques restent encore peu accessibles aux pays en voie de développement, en raison de leur coût élevé et de leur complexité. Ce dernier point limite fortement des pays comme la Chine ou l’Inde, qui disposent de peu d’entreprises qualifiées et automatisées. À cela s’ajoute un cadre réglementaire souvent incomplet ou inadapté. En bref, il devient urgent de développer des technologies de démontage durables pour les WPCB dans les pays en développement d’Asie et d’Afrique.

### 3.1.3 L’évolution de la recherche scientifique sur les DEEEs

Comme nous avons pu le voir, la croissance inquiétante des DEEEs et leur mauvaise gestion de fin de vie entraîne une urgence mondiale qui est par ailleurs visible si l’on s’intéresse à l’évolution des articles et brevets scientifiques relatant cette thématique. L’article [22] recense de nombreux brevets classés en fonction du mode de recyclage des DEEE. On y retrouve également les graphiques de la figure 3 qui permettent de visualiser l’évolution de la quantité de brevets/articles publiés dans le domaine. Nous pouvons alors voir que la recherche est en plein essor depuis les années 2000 de manière globale. En revanche, si l’on se concentre uniquement sur la séparation et au retrait des ECs, la tendance est moins favorable : les publications scientifiques dans ce domaine sont moins nombreuses et n’augmentent pas aussi nettement, ce qui laisse penser que ce champ reste encore peu exploré et mérite des recherches approfondies dans une optique de valorisation complète et durable.

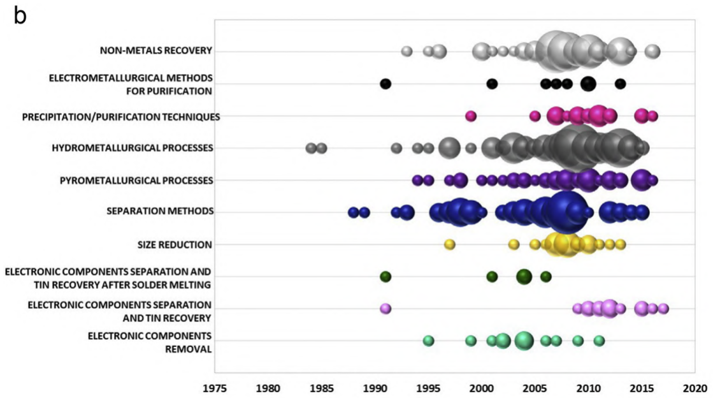
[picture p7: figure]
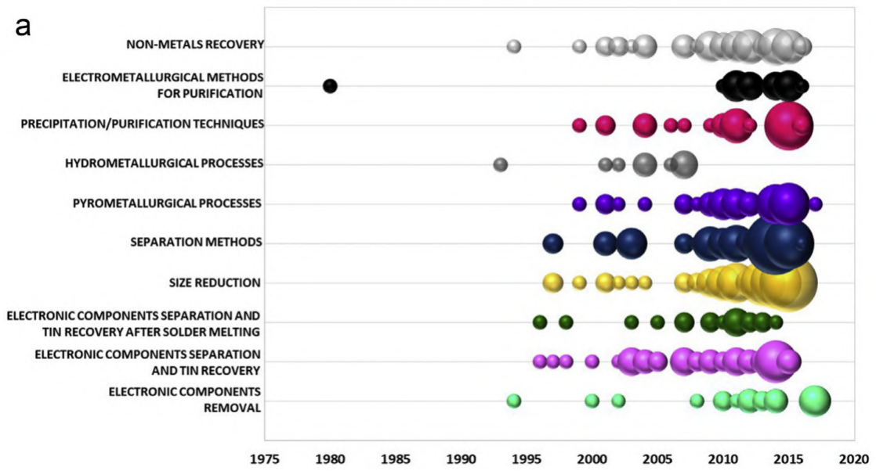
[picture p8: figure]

Figure 3 – Comparaison entre l’évolution technologique (a) et scientifique (b) des procédés de valorisation des cartes

électroniques en fin de vie.

### 3.2 Le traitement actuel des DEEE

Le démantèlement illégal des DEEE, notamment exportés vers des pays en développement, est souvent réalisé sans précaution, provoquant une grave pollution et des risques sanitaires majeurs, comme à Agbogbloshie. Environ 60% de nos DEEE échappent ainsi au traitement réglementé.[9]
À l’inverse, dans les centres de recyclage officiels, les déchets sont manipulés de manière plus sûre pour limiter la pollution, mais la priorité reste l’élimination plutôt que la revalorisation. Les WPCB y sont généralement broyés sans tri préalable, rendant difficile la récupération des métaux rares pourtant stratégiques [18].
Approximativement 70% des WPCB sont composés d’une pièce électronique comprenant un PCB, avec plusieurs ECs montés sur la carte [2]. Le PCB est principalement composé de cuivre et de résine époxy renforcée de fibres de verre. Les ECs eux, peuvent être des résistances, des transistors, des microcontrôleurs, etc. [5], qui contiennent surtout des métaux de base (Cu, Fe et Al), des métaux nobles (Au et Ag), des métaux rares (Se, Ge et Te) ainsi que des métaux toxiques (Pb, Cd, Hg et As). Ces métaux présentent un intérêt plus ou moins important selon leur rareté, leur complexité d’extraction ou encore leur composition. Leur traitement représente également un défi environnemental majeur en raison de la présence de substances toxiques [18]. Ainsi, un bon recyclage des WPCB nécessite le désassemblage des ECs, afin qu’ils puissent être recyclés séparément de la carte nue. Ce principe de base est à la source de plusieurs démarches actuelles visant à traiter la fin de vie des DEEE.
En clair, la gestion des DEEE constitue un véritable défi à l’échelle mondiale. Le modèle actuel de production et de consommation, basé sur le schéma « extraire-fabriquer-jeter », n’est pas durable. Une réorientation vers une électronique circulaire et responsable devient indispensable, notamment face à la rareté croissante des Matières premières critiques (CRMs) et à la hausse exponentielle des DEEE [2].

### 3.2.1 Récupération des ECs

En 2022, selon UNITAR [7] seulement 22,3 % des DEEEs produits ont été correctement collectés et recyclés. Parmi ce petit quart de nos DEEE, uniquement une faible partie des matériaux les constituants sont récupérés. La plupart des méthodes de recyclage posent un gros problème en termes de pollution et de capacité à revaloriser tous les matériaux. Ainsi, plusieurs articles proposent des solutions pour recycler les PCB de manière plus respectueuse et valorisante. L’approche susceptible de nous permettre d’atteindre les meilleurs objectifs en termes de revalorisation est alors la récupération en vue de la réutilisation. Cette méthode pourrait permettre plusieurs choses :
— Favoriser l’économie circulaire
Un des grands objectifs de la récupération d’ECs est de pouvoir rallonger leur cycle de vie. L’article [25] recense différents travaux afin de mettre en lumière les diverses études menées sur le sujet, ainsi que les impacts environnementaux potentiels associés. Des méthodes et outils permettant de quantifier et d’analyser ces incidences tout au long du cycle de vie sont ainsi abordés, dans le but de réaliser des analyses de cycle de vie (LCA).
— Préserver des ressources critiques
Certains matériaux rares sont présents dans les ECs ainsi pouvoir réutiliser ces derniers nous permettrait de réduire notre utilisation de CRMs. La récupération est alors la meilleure alternative pour préserver les ressources critiques, étant donné que le recyclage ne permettra pas une revalorisation à 100% [14]. — Améliorer la résilience face aux crises
Les équipements électroniques contiennent des matériaux rares tels que l’or, l’argent, le platine ou des éléments qui ne peuvent être trouvés que dans des pays politiquement instables [4]. Ainsi, notre production d’appareils électroniques peut être directement impactée par une crise ou une guerre. Pouvoir récupérer des ECs, directement de nos DEEE, afin de les réutiliser sans avoir à en fabriquer de nouveaux, pourrait nous permettre de pallier cette dépendance.
— Résoudre les problèmes d’approvisionnement :
La récupération et la réutilisation pourraient également permettre de résoudre les problèmes d’obsolescence, de longs délais de livraison, de déchets électroniques et de pénuries d’ECs.
— Réduction de la mortalité infantile des ECs
Tout EC est associé à une courbe de probabilité de mortalité. On remarque alors que ces derniers font face à une hausse de leur probabilité de défaillance en début de vie, ce qui correspond à la mortalité infantile. Nous pouvons retrouver sur la figure 4 cette zone critique qui arrive au début de vie d’un EC.

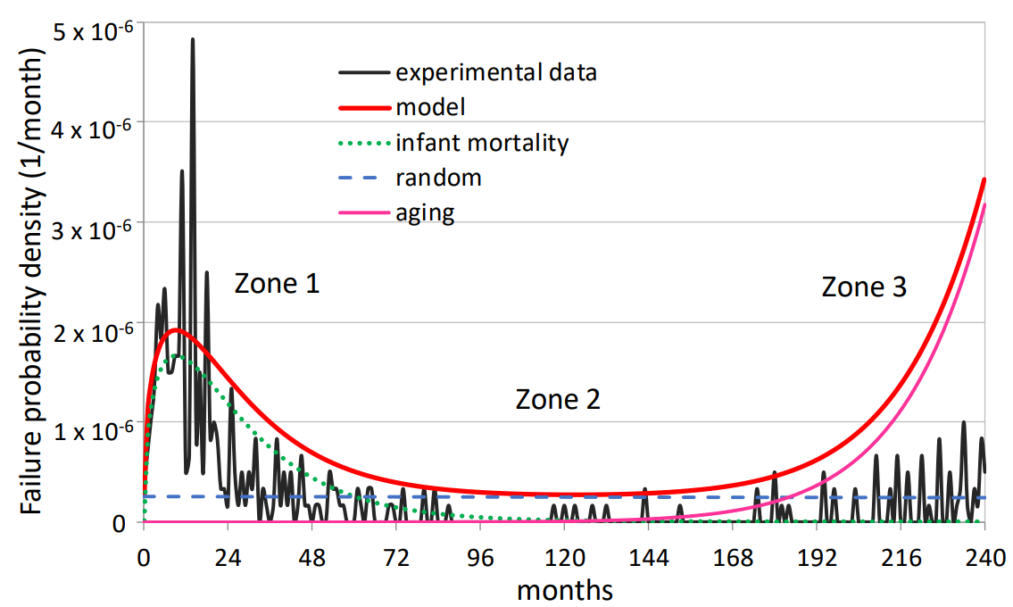
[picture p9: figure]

Figure 4 – Taux de défaillance expérimental qui peut être subdivisé en trois zones : mortalité infantile (1), échec

aléatoire (2) et vieillissement (3)
Cette zone nous intéresse vis-à-vis de la récupération d’ECs. En effet, le fait que l’EC récupéré ait déjà survécu à la mortalité infantile augmente la fiabilité de l’EC utilisé par rapport à un EC neuf. En somme, si la récupération et la réutilisation d’un EC se déroulent bien, il pourrait ainsi devenir intéressant d’utiliser des ECs de seconde vie [4].

### 3.3 Les méthodes de récupération des ECs

La récupération des ECs représente de nombreux challenges, nous pourrons les évoquer dans un premier temps avant d’aborder les différentes étapes que constitue la récupération des ECs.

### 3.3.1 Contraintes et enjeux de la récupération

Les principaux défis incluent :
— La traçabilité des ECs : Afin de pouvoir évaluer la durée de vie restante d’un EC, un simple test de bon fonctionnement n’est pas suffisant. Des informations sur ses conditions d’utilisation sont nécessaires pour estimer son état et pour pouvoir assurer une certaine fiabilité. Ainsi, la traçabilité des ECs est primordiale si nous souhaitons étendre le marché de la récupération et de la réutilisation des ECs présents sur nos DEEE. L’article [1] présente une base de données et une application web permettant de retracer la vie d’ECs depuis leur fabrication jusqu’à leur recyclage. Ceci offre alors la possibilité de faire de meilleurs choix quant à la récupération et à la réutilisation des ECs. D’autres parts, la base de donnée donne également des informations sur le PCB en lui-même et permet de donner des informations sur les ECs critiques (composés de matériaux dangereux ou rares) présents sur la carte. Ces informations pourraient alors être utilisées pour choisir quels ECs sont à récupérer en priorité.
— Estimer la durée de vie avant récupération d’un EC : Un point important dans la réutilisation d’ECs est de pouvoir tester l’EC afin d’estimer sa fiabilité. Les principales causes de vieillissement d’un EC viennent des températures auxquelles il a été exposé, des stress mécaniques ou chimiques qu’il a subis ou encore de son exposition à des vibrations, à la corrosion ou à l’humidité. Ainsi, des tests poussés ont pu être réalisés [19] dans le but d’étudier le fonctionnement d’un EC. Cette étude s’est basée sur la température de l’EC au cours de son utilisation à l’aide d’une caméra infrarouge. Grâce aux données récupérées, un algorithme de prédiction de la durée de vie restante d’un EC a été mis au point. Ces informations pourraient permettre le ciblage des ECs intéressants à récupérer dans une optique de réutilisation.
— La miniaturisation croissante : L’évolution de l’électronique tend vers la conception et l’utilisation d’ECs de plus en plus petits. En termes de réutilisation, cette miniaturisation croissante a des répercussions. La manipulation de micro-composants exige une grande précision, une grande fiabilité et un rendement élevé. À cette échelle, les forces d’adhésion entre l’EC et le préhenseur entravent souvent le processus lors du relâchement, limitant ainsi les performances globales des systèmes conventionnels. L’article [24] introduit un système fonctionnel permettant la récupération et un relâchement sans problème de micro-composants dans l’objectif de leur réutilisation.

— Manque de traçabilité, de normalisation et de structuration des chaînes de revalorisation L’absence de déclarations de qualité pour les ECs récupérés, ou pour ceux dont la durée de vie est prolongée, freine leur réintégration. À cela s’ajoute le manque de normalisation dans la conception des systèmes pour faciliter leur désassemblage, ainsi qu’une structuration encore immature des infrastructures techniques et logistiques capables de prendre en charge la revalorisation de ces dispositifs [19].
— Permettre la récupération : Finalement, la récupération rencontre également ses défis afin de récupérer sans endommager tout en ayant une cadence suffisante pour qu’elle soit rentable. Elle doit aussi être respectueuse de l’environnement. Un des gros objectifs de la récupération est de réduire l’impact environnemental des produits. Ainsi, elle ne doit pas être plus coûteuse environnementalement parlant que la fabrication. D’autre part, des questions se posent sur l’échelle à laquelle la récupération pourrait se faire pour que la remise sur le marché des ECs soit efficace. Une possibilité, à grande échelle, pourrait alors être que ce soit les fabricants des ECs ou des cartes électroniques qui s’en chargent. Dans cet esprit, ces derniers auraient directement la connaissance de ce qu’on subit les ECs pendant leur fonctionnement, ce qui faciliterait l’estimation de leur durée de vie et ainsi que la remise sur le marché des ECs, directement avec leur structure déjà fonctionnelle.
À une échelle plus réduite, des entreprises faisant du prototypage pourraient faire de la récupération à partir de leur prototype obsolète afin de les réutiliser dans de nouveaux projet, comme cela peut-être le cas dans le laboratoire LAIC.

### 3.3.2 Tri et identification

L’identification et le tri constituent une première étape essentielle dans la récupération d’ECs. L’identification permet de localiser les ECs, d’évaluer leur état, leur type, ou encore leur dangerosité [8]. Le tri lui permet de choisir quel EC démanteler, dans quel ordre et avec quel outil.
Afin de mettre en place cette première étape, différentes approches sont utilisées. Les systèmes de vision par ordinateur, comme ceux décrits dans [11] et [8], s’appuient sur l’analyse de la forme, la couleur ou le marquage des ECs, en les comparant à une base de données, afin d’identifier les éléments réutilisables ou sensibles. D’autres méthodes, plus avancées, s’appuient sur des réseaux de neurones comme les modèles YOLO. Ces derniers permettent de reconnaître automatiquement les ECs, même à partir de peu d’exemples, grâce à l’apprentissage dit "few-shot" [23], [16]. Enfin, une solution alternative consisterait à intégrer dès la conception de la carte un identifiant unique, donnant accès à toutes les informations utiles au démontage ou à la valorisation du PCB, comme le propose l’approche Passeport-PCB décrite dans [1].
Ces solutions présentent un gros intérêt lorsque nous n’avons aucune information sur les cartes récupérées. Dans notre cas d’étude, nous considérons avoir accès aux fichiers de fabrication, des cartes électroniques, qui contiennent la position des différents ECs. Ainsi, dans notre cas, nous n’aurons uniquement besoin de référencer la position du premier EC à récupérer ainsi que d’aligner le PCB sur les axes de la machine pour en déduire la position des autres. Un support de carte sera alors nécessaire pour garder cette dernière en position tout au long de la récupération et garantir la bonne récupération de l’ensemble des ECs. Cette solution est facilement implémentable au sein du laboratoire et nous permettra de gagner du temps pour se consacrer pleinement aux phases de dessoudage et de désassemblage.

### 3.3.3 Dessoudage

Suite à cette première étape, nous pouvons aborder le retrait à proprement parler des ECs de la carte. Cette phase combine généralement le dessoudage et le désassemblage. Ces deux étapes consistent d’une part à utiliser une source de chaleur pour faire fondre la brasure lors du dessoudage, et d’autre part à un système d’extraction des ECs pour assurer le désassemblage [17]. Nous nous intéresserons dans un premier temps aux méthodes de dessoudage indépendamment de celles de désassemblage.
Cette étape est critique dans le processus de récupération, car elle a un impact direct sur la qualité des ECs récupérés. La température doit être rigoureusement contrôlée afin d’éviter toute détérioration des ECs. De plus, la présence d’humidité doit être surveillée pour éviter le phénomène dit de "pop-corn" qui se produit lorsque l’eau piégée dans le matériau d’encapsulation se transforme en vapeur sous l’effet de la chaleur. Cette réaction provoque alors une déformation ou un soulèvement de la surface de l’EC empêchant sa revalorisation [28].

Le dessoudage des ECs a été largement étudié, avec d’une part des approches visant uniquement à séparer les ECs de la carte, sans se soucier de leur état après récupération, et d’autre part des recherches orientées vers des méthodes plus douces pour préserver l’intégrité des ECs. L’article de [15] présente un éventail complet de ces techniques, illustré dans le tableau 1. Ces dernières sont comparé selon leur Investissement initial (CAPEX) et Coût opérationnel (OPEX) ainsi que selon leur avantages et inconvénients

Procédé | CAPEX | OPEX | Avantages | Inconvénients
Démantèlement manuel | + | ++++ | Facile à mettre en œuvre ; Démantèlement sélectif | Travail manuel difficile ; Besoin de main-d’œuvre ; Processus lent ; Polluant
Couteau de découpe de surface | ++ | + | Non polluant ; Taux de démantèlement élevé | Les WPCBs sont traitées une par une
Chauffage brut | ++ | + | Grande capacité | Émissions toxiques ; Dommages thermiques aux ECs
Radiateurs infrarouges | ++ | + | Taux de démantèlement élevé | Petits volumes ; Dommages thermiques aux ECs
Chauffage à air chaud | ++ | ++ | Taux de démantèlement élevé ; Peu d’entretien ; Non polluant | Faible précision de contrôle ; Faible efficacité énergétique
Bain de soudure chauffant | ++ | +++ | Taux de démantèlement élevé | Difficile à automatiser ; Émissions de fumées toxiques ; Conditions de travail dangereuses
Chauffage par fluide chaud | ++ | ++ | Taux de démantèlement élevé ; Haute efficacité thermique | Génération de déchets fluides et fumées toxiques
Centrifugation chauffée | ++ | ++ | Taux de récupération élevé de la soudure | Haute température ; Dommages thermiques aux ECs
Dissolution de la soudure | + | ++ | Processus sélectif ; Séparation des éléments de soudure | Nécessite des traitements supplémentaires ; Produits chimiques dangereux utilisés
Traitement hydrothermal et supercritique | +++ | ++ | Cible métaux ou résines ; Aucun produit toxique libéré ; Réactifs réutilisables | Ne peut pas cibler la soudure ; Nécessite d’autres traitements de démantèlement
Traitement de la résine époxy | ++ | ++ | Récupère circuits fonctionnels ; Produits chimiques recyclables | Besoin d’autres processus de démantèlement ; Produits chimiques dangereux utilisés
Démantèlement robotisé | +++ | + | Démantèlement et tri combinés ; Faible besoin en main-d’œuvre | Faible rendement

Fragmentation par
concasseur à impulsions
électriques haute tension
++++ | ++ | Grande capacité ; Non polluant

Faible efficacité énergétique ; Investissement initial
coûteux

Table 1 – Comparaison des méthodes de dessoudage
Certaines de ces méthodes sont néfastes pour l’environnement, comme le "bain de soudure chauffant" ou la "dissolution de la soudure". D’autres peuvent endommager les ECs : par exemple, la méthode dite "couteau de découpe de surface", qui peut laisser les pattes des ECs sur la carte, les rendant ainsi inutilisables.
Parmi les techniques listées, nous détaillerons celles qui semblent les plus en phase avec notre objectif : réduire l’impact environnemental des DEEE en maximisant la récupération et la revalorisation des ECs fonctionnels.

Afin de dessouder les ECs nous nous intéresserons essentiellement aux méthodes de chauffe qui sont davantage respectueuses de l’environnement. Ainsi, pour dessouder les ECs d’une carte, il nous sera nécessaire d’atteindre une température au moins supérieure à la température de fusion de la brasure. Dans le but d’augmenter les performances de dessoudage, il est possible de jouer sur la méthode de chauffe ou encore sur la température de consigne. Le type de brasure utilisé a également un impact sur le résultat de notre dessoudage. L’étude [34] au sujet de la température à appliquer sur les ECs a montré qu’au-delà de 250°C, une hausse de température n’améliore plus significativement la vitesse de fusion de la brasure. En revanche, des gaz toxiques peuvent apparaître dès 280°C. Ainsi, une température trop élevée peut être néfaste en termes de pollution et risque par ailleurs d’endommager les ECs. Notre méthode de chauffe devra donc permettre une montée en température performante afin d’avoir un dessoudage efficace tout en étant homogène pour éviter des zones trop chaudes qui pourraient endommager les ECs ou des zones trop froides qui ne permettraient pas un dessoudage performant. Par ailleurs, certains ECs sont fixés à la fois par brasure et adhésif, ce qui nécessite une analyse précise des matériaux pour adapter le procédé de dessoudage, optimiser la récupération et limiter l’impact environnemental.
Précaution en température pour assurer le non-endommagement de ECs
Comme énoncé dans le paragraphe précédent, la température est un point critique du dessoudage des ECs. Cette problématique a un impact sur l’environnement, comme nous avons pu l’introduire en amont, mais également sur la facilité de retrait des ECs et surtout sur leur endommagement. Afin d’assurer un réemploi des ECs, une courbe de température doit être suivie. Cette dernière s’inspire largement des courbes de température suivies lors du brasage des ECs. L’objectif avec le dessoudage sera alors de suivre les mêmes caractéristiques dans le but d’assurer que les contraintes infligées aux ECs soient les mêmes et par suite qu’elles soient supportables par ces derniers. Ainsi, si l’on s’intéresse aux prérogatives données par des fabricants d’ECs, on peut trouver des courbes de température telles que celle figure 5 qui est conseillée par Vishay, fabricant de semi-conducteurs discrets et d’ECs passifs. Le document de recommandation détaillé se trouve en annexe 34.

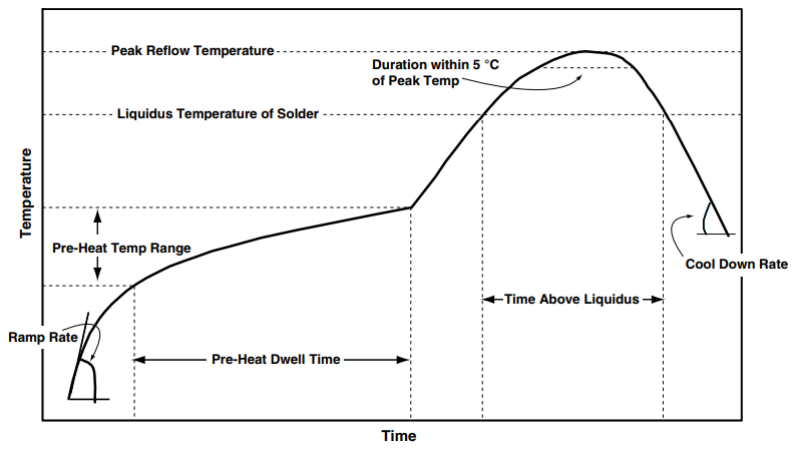
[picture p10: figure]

Figure 5 – Courbe de température brasage ECs

Nous pouvons alors remarquer que de nombreux paramètres sont définis. Le temps de chauffe, les pentes des courbes et les températures sont primordiales pour ne pas endommager les ECs et assurer un bon dessoudage.

L’article [30] présente une étude visant à rendre compte de l’impact du choix des paramètres de température et du temps de chauffe. Les paramètres expérimentaux sont visibles sur la figure 6. Les impacts étudiés concernent la qualité de la brasure lors du soudage des ECs. Ainsi, l’article ne fournit pas d’informations directes sur les effets de ces paramètres pour le dessoudage, mais il constitue une bonne indication des courbes suivies pour le soudage, ainsi que de l’influence des températures de plateau lors de cette étape.
Dans le cadre de notre étude, cet article apporte donc des éléments précis sur les caractéristiques envisageables pour la courbe de dessoudage à adopter. Combiné aux informations fournies par Vishay, il nous donne une première idée des paramètres à sélectionner.

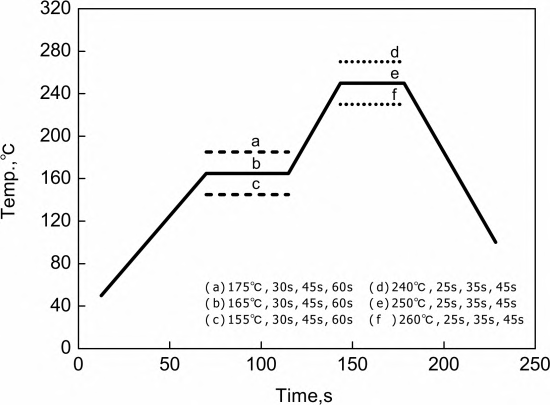
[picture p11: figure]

Figure 6 – Impact température brasage ECs

Méthodes de dessoudage automatisables
Pour envisager une implémentation simple et efficace d’une station de dessoudage automatisée, il est essentiel d’analyser les différentes technologies disponibles selon leur performance thermique, leur accessibilité technique et leur impact sur la réutilisabilité des ECs.
Nous pouvons constater que les différentes méthodes ont des avantages et des inconvénients différents, et que le choix de la méthode de dessoudage appropriée en fonction des différents types de cartes est l’étape cruciale de la réutilisation des ECs sur les WPCB [34]. Le tableau 2 permet une bonne appréciation globale des enjeux pour chaque méthode.
Méthode | Coût | Performance thermique | Complexité | Réutilisabilité des ECs
Laser [10] | Élevé | Excellente | Élevé | Excellente
Air chaud [15] | Faible | Faible | Faible | Moyenne
Air chaud + tubes [29] | Moyen | Bonne | Moyenne | Bonne
Infrarouge (IR diffus) [32] | Moyen | Moyenne | Moyenne | Moyenne

Table 2 – Comparatif des méthodes de dessoudage pour une station automatisée

Dans notre cas d’étude, la méthode laser est écartée en raison de la complexité qu’elle implique en termes d’intégration et de sécurité. Les trois autres méthodes restent donc à envisager. La méthode à air chaud pourrait cependant s’avérer la plus intéressante si l’on parvient à obtenir un système de chauffe suffisamment homogène. Vis-à-vis de la littérature, il nous est difficile de trancher sur une solution. Une étude plus poussée sera présentée sur ce choix dans la suite du rapport.

### 3.3.4 Désassemblage

Afin de procéder à la récupération des ECs, le dessoudage doit être combiné à un désassemblage. Plusieurs méthodes sont alors envisageables, le démantèlement mécanique (préhension, aspiration sous vide, vibration et impact), le démantèlement par jet de gaz et l’utilisation de la gravité, de la force centrifuge ou de cisaillement, etc. [34]. Certaines de ces méthodes sont compatibles avec une industrialisation et/ou permettent le retrait d’une variété d’ECs définis. Par rapport à ce dernier point, l’utilisation d’une force verticale serait par exemple plus efficace que l’utilisation d’une force horizontale lors de l’enlèvement des dispositifs traversant (THD), tandis qu’une force horizontale serait plus efficace lors de l’enlèvement des dispositifs montés en surface (SMD)s.

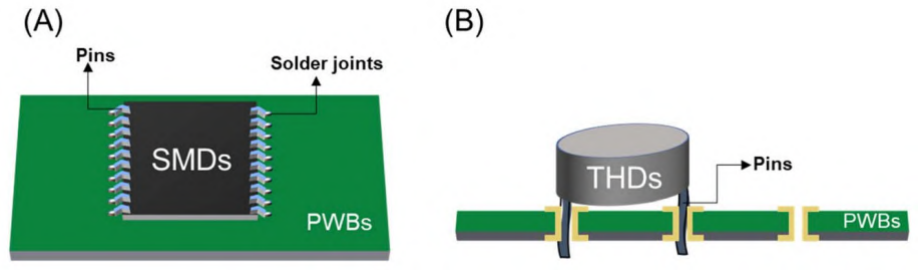
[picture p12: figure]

Figure 7 – Les deux types de dispositifs pour les ECs : (A) SMD et (B) THD

D’autre part, au sein même d’un type d’EC (THD vs SMD), le mécanisme utilisé peut grandement varier. Si nous nous intéressons aux SMDs, les plus petits ECs ne demanderont pas les mêmes spécificités que les plus gros. Ainsi, la solution choisie peut en être fortement affectée. Similairement pour les THDs, si les broches de l’EC ne sont pas pliées, ce dernier peut être démonté avec une faible force ou accélération, et même se détacher de lui-même sans force extérieure, mais dans le cas de broches THD pliées, la force d’extraction nécessaire est plus importante et s’accentue avec l’augmentation de l’angle de pliage des broches [31]. Ainsi, le bon désassemblage des ECs va dépendre des ECs présents sur la carte, de la méthode retenue et également de la méthode de dessoudage employée. Grâce à cet état de l’art, nous présenterons différentes méthodes de désassemblage qui ont pu être mises en place. Ces différents systèmes se basent sur le principe d’un pick and place inversé. Ainsi, ils seront associés à un système de vision ou autre permettant la localisation des ECs ainsi que leur type dans certains cas.
Comparatif des différentes méthodes de désassemblage
Le tableau 3 ci-dessous permet de comparer les différentes méthodes de désassemblage trouvées dans la littérature.
Technique | Application | Avantages | Inconvénients
Désassemblage flexible [10] [11] | Multi-composants | Très flexible, automati-sable | Systèmes complexes et coûteux
Aspiration [8] | Composants SMD | Simple, peu coûteux | Limité aux ECs légers
Mâchoires parallèles [8] [31] | Composants THD | Retrait précis, force modu-lable | Moins adapté aux petits ECs
Micro-préhenseur à vide [24] | Micro-SMD | Précis, adapté aux ECs fra-giles | Système complexe et coûteux
Système vibratoire [29] | ECs variés | Rapide, automatisable | Inefficace pour certains ECs

Table 3 – Résumé des techniques de désassemblage

Les différentes solutions présentées sont plus ou moins complexes. Au vu du temps et des moyens que j’ai à ma disposition, j’ai dû rapidement faire le choix de simplifier le problème. Ainsi, j’ai choisi de me concentrer sur les ECs que l’on trouve en majorité sur les cartes électroniques de nos jours et qui représentent un intérêt pour la récupération. Cette limitation dans le panel d’ECs existant sur les cartes électroniques était nécessaire dans le cadre du stage, mais pourra par la suite être élargie. Ce choix m’a ainsi permis de cibler les ECs SMDs qui sont de plus en plus utilisés et qui seront en termes de répétabilité plus fiables à la récupération. J’ai également fait le choix d’évincer les micro-composants qui ne représentent pas un intérêt suffisant à la récupération, autant d’un point de vue environnemental qu’économique. Ainsi, nous écartons rapidement la technique de désassemblage flexible. En effet, pour le moment, nous allons nous concentrer sur un seul type de préhenseur pour le désassemblage. La technique micro-préhenseur à vide et la technique mâchoire parallèle sont par ailleurs écartées au vu du choix présenté en amont. Ainsi, il nous reste la méthode par vibration et par aspiration. La différence entre les deux, au vu des objectifs que nous avons, est la rapidité, la simplicité et la répétabilité. La rapidité ne fait pas partie de nos critères majeurs actuels, ainsi j’ai fait le choix de m’orienter vers la technique de désassemblage par aspiration qui est meilleure vis-à-vis des deux autres critères. Ce choix est propre au stage et aux restrictions qu’il incombe.

### 3.3.5 Test et qualification

Finalement, la dernière phase dans notre processus de récupération d’ECs est celle de test de bon fonctionnement. Cette dernière thématique permet de vérifier que les ECs n’ont pas été endommagés.
Évaluation de la durée de vie résiduelle
Au sein d’un système, lorsque le produit arrive en fin de vie, les sous-systèmes ont des valeurs résiduelles différentes. La valeur résiduelle pour un EC électronique correspond à la valeur restante de ce dernier après un certain temps d’utilisation dans certaines conditions. Ainsi, afin de revaloriser chaque sous-système, il est primordial d’arriver à estimer cette valeur résiduelle. L’article [19], propose une étude permettant de l’estimer. Pour ce faire il introduit deux variables : Le taux de réutilisation Rrate, indiquant le nombre de fois où les ECs peuvent être réutilisés successivement, ainsi que l’empreinte environnementale et le coût des processus de réutilisation qui lui-même regroupe trois autres critères, le nombre d’outils de démontage utilisés, le temps passé et l’énergie consommée en plus de l’estimation de l’empreinte environnementale. La valeur résiduelle peut alors être calculée lors de la phase de diagnostic, juste après la « dernière » utilisation.
Les principaux indicateurs permettant d’estimer la valeur résiduelle d’un EC sont les conditions d’utilisation de ce dernier, correspondant à la connaissance des contaminations, humidité, vibrations, température auxquelles il aurait pu être exposé. Afin d’avoir accès à ces informations, l’article [19] propose l’utilisation d’une caméra infrarouge, permettant d’avoir un visuel sur les températures que subissent les ECs d’une carte.
Cette notion de traçabilité est également abordée dans l’article [1]. Celui-ci propose un système de traçabilité donnant accès à une base de données cloud regroupant des informations telles que la durée de vie moyenne d’un EC, son historique d’utilisation, son exposition à l’humidité ou encore les températures auxquelles il a été soumis. Ces données, s’il est possible de les collecter, permettrons ensuite d’évaluer sa fiabilité une fois l’EC récupéré.
Test de bon fonctionnement
Afin de détecter les défauts d’un EC, les auteurs de l’article [12] ont appliqué des contraintes thermiques sur une puce préalablement extraite d’une carte électronique, puis réintégrée sur une nouvelle. L’objectif de cette démarche était d’analyser les caractéristiques de l’EC avant et après sollicitation. L’analyse menée comprenait notamment l’utilisation de rayons X, la mesure des composés intermétalliques, ainsi que la réalisation de tests fonctionnels sur les nouveaux dispositifs. Les résultats de l’étude ont ainsi démontré que les procédés de récupération, de reconditionnement et de réintégration permettent une remise sur le marché des ECs. L’article [5] présente une méthode de test plus simplifiée, se concentrant uniquement sur des tests basiques de bon fonctionnement à un instant donné. Une table (annexe 35) recense les critères de réutilisation des ECs ainsi que les options de recyclage disponibles. Ces vérifications permettent de s’assurer que l’EC est encore fonctionnel, mais elles restent peu robustes, car elles ne fournissent aucune information sur la fiabilité à long terme ni sur la valeur résiduelle de l’EC.

### 3.3.6 Conclusion sur les méthodes de récupération des ECs

Nos quatre thématiques offrent chacune de nombreuses méthodes, plus ou moins adaptées à notre cas d’étude. Une vision globale de ces dernières permet de prendre conscience de l’étendue des recherches existantes et de la nécessité d’approfondir celles-ci afin d’aboutir à un système à la fois fiable et flexible. D’autres thématiques pourraient également apparaître dans un système complet, telles que des étapes de tri ou de remise en état des ECs. L’article [33] présente notamment une structure de contrôle permettant de déterminer la meilleure stratégie de démantèlement du PCB. Dans la suite du rapport, nous présenterons les différentes solutions qui ont été retenues suite à cet état de l’art.

### 3.4 Quels ECs cibler pour quels impacts ?

L’un des objectifs de l’état de l’art était par ailleurs d’étudier l’impact des ECs en termes de fabrication, mais aussi de se renseigner sur l’intérêt de la récupération en fonction des ECs ciblés. Nous nous intéresserons donc aux ECs qui seraient les plus intéressants à récupérer d’un point de vue économique, environnemental et sociétal.

### 3.4.1 Impact économique et social

Intéressons-nous ici à la réutilisation des ECs dans leurs globalités. La récupération des ECs de nos DEEE pourrait avoir un impact économique et sociétal. En effet, l’article [5] présente une nouvelle industrie qui pourrait apparaître en Chine sous le nom de “Electronics Component Testing Industry”. Cette apparition pourrait permettre une augmentation de l’emploi, les acheteurs auraient par ailleurs des prix sur leurs objets électroniques défectueux qui pourraient alors être rachetés par cette industrie. Cela pourrait donc créer un impact positif sur la situation économique des citoyens d’un pays puisque le montant total de l’argent qu’ils dépenseront pour des gadgets électroniques diminuera du fait que leurs produits auront toujours de la valeur pour être revendus à leur fin de vie. D’un point de vue de la santé, les risques seront aussi réduits du fait d’une meilleure gestion des déchets.
En Europe, l’article [2] montrent que selon des études, jusqu’à 50% des utilisateurs préféreraient utiliser des produits remis à neuf et que l’exploitation de ce potentiel grâce à de nouveaux modèles commerciaux pourrait générer de nouveaux emplois et renforcer l’économie (européenne) de 115 à 325 milliards d’euros supplémentaires.
L’article [29] présente un cas concret de récupération d’ECs. Une étude a été menée afin d’évaluer le coût de cette opération à l’aide du système proposé. En supposant que 16 tonnes de WPCB soient traitées par cette méthode, avec une puissance électrique de l’équipement de 50 kW, et en prenant en compte les coûts d’amortissement ainsi que la consommation d’énergie, le coût total de la récupération a été estimé à environ 4,61 $ par tonne de WPCB. De plus, ce procédé génère très peu de substances toxiques et n’a pratiquement aucun impact négatif sur la santé des travailleurs ni sur l’environnement. En somme, cette application a donné des résultats satisfaisants du point de vue environnemental, mais aussi économique, ce qui est encourageant pour la suite.
Si l’on se recentre à présent à l’échelle d’un EC ou d’un ensemble d’ECs présents sur une carte, l’estimation du coût va dépendre du nombre d’outils de désassemblage utilisés, du temps et de l’énergie consommés. Ce coût doit alors être amorti par la remise sur le marché de l’EC. Des entreprises telles que Retronix [20] ou encore Resale components[21] ont par exemple réussi à trouver du profit dans ce système en ciblant leur récupération sur des ECs spécifiques à haute valeur ajoutée, par exemple des microprocesseurs, sur des jeux de WPCBs identiques. En clair, à l’échelle du stage, il nous est difficile de faire un choix vis-à-vis du coût de récupération étant donné la quantité de paramètres à considérer, néanmoins nous essayons de cibler des ECs qui ont un certain coût d’achat, ce critère nous permet d’enlever les ECs qui ne seraient pas financièrement rentables à revaloriser.
L’article [4] fait part d’une étude afin de quantifier le taux de défaillance d’un EC neuf et de seconde vie ainsi que le prix que pourraient avoir différents ECs. Cette étude pourra être une bonne base pour la suite du projet.

### 3.4.2 Impact environnemental

En l’absence d’alternatives viables et d’options de recyclage, les DEEE mis au rebut risquent de finir dans des décharges. Ceci est un vrai problème environnemental étant donné que les substances dangereuses contenues dans les produits électroniques contaminent, entre autres, les eaux souterraines. Ainsi, limiter cette fin de vie au maximum en démocratisant la récupération des ECs et le recyclage propre pourrait nous permettre de reprendre le contrôle sur nos pollutions liées à la fin de vie de nos équipements électroniques. L’article [26] défend ainsi ce paradigme et propose un modèle permettant de calculer le score de l’impact environnemental (EI) d’un produit en identifiant les matériaux contenus par ce dernier et en quelle quantité. Dans une structure de pondération par défaut, une pondération de 40% est attribuée à la santé humaine, 40% à la qualité des écosystèmes et 20% à la consommation de ressources. Le résultat final est exprimé sous la forme d’un score unique (indicateur) qui reflète l’impact environnemental global en agrégeant les trois catégories de dommages. 1 Pt représente un millième de la charge environnementale annuelle d’un habitant européen moyen. Les scores Eco-Indicator utilisés dans ce système correspondent à l’impact lié à la phase de fabrication des matériaux.

Le tableau 4 reprend les scores trouvés et permet de se rendre compte des différences d’EI que peuvent avoir les DEEE.

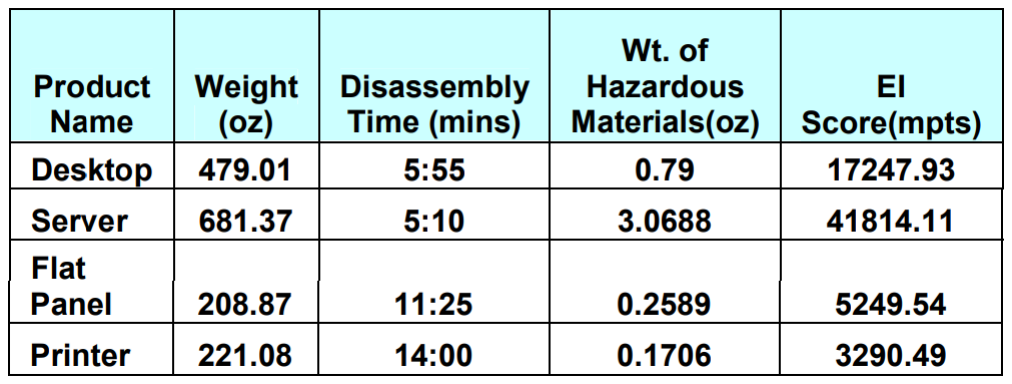
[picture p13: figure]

Table 4 – Score EI pour différents produits électroniques
Nous pouvons également retrouver dans le tableau 5 ci-dessous les scores EI de certains matériaux. Il est alors possible de voir que l’or présente un score EI très élevé, signifiant un fort impact environnemental. Toutefois, son utilisation se limite à de très faibles quantités. Ainsi, les ECs contenant de l’or ont un score élevé qui fluctue grandement en fonction de leur teneur d’or. Bien que cet élément soit crucial pour notre objectif de récupération, cela ne minimise pas l’importance d’autres ECs, comme les condensateurs, qui sont souvent constitués de tantale et/ou d’aluminium en plus grande concentration. Ce facteur compense alors le score EI de ces deux matériaux qui sont bien inférieurs à l’or.
Matériau | Utilisation typique | EI-99 (Pt/kg)
Aluminium (primaire) | Boîtiers, dissipateurs de chaleur | 3,17
Tantale | Condensateurs | 45
Cuivre | Fils, pistes de circuits imprimés | 0,458
Or | Connecteurs, circuits intégrés | 1290
Argent | Soudures, conducteurs haute performance 74
Étain | Soudure sans plomb | 1,22
Plastique ABS | Boîtiers, connecteurs | 0,09 - 0,15
Silicium | Puces électroniques, semi-conducteurs | 0,21 - 0,35
Nickel | Alliages, batteries | 2,73
Lithium | Batteries (Li-ion) | 5,92
Cobalt | Batteries, alliages | 11,76
Verre (fibre/verre simple) Écrans, substrats PCB | ∼0,09

Table 5 – Valeurs EI-99 de matériaux utilisés en électronique

### 3.4.3 Impact des métaux critiques

Si nous nous intéressons à présent aux CRMs nous pouvons comprendre que leur recyclage est très important. Nous retrouvons ainsi les différents enjeux qu’ils représentent [11] :
— Atteindre les objectifs globaux de l’économie circulaire
— Réduire la charge toxique sur les sites d’extraction, de transformation et de fabrication, ainsi qu’autour de ces sites
— Minimiser la dégradation des sols, des habitats naturels et des conditions de vie, tant pour les êtres humains que pour les espèces animales et végétales en danger
— Réaliser des économies pour la fabrication (en tenant compte de la hausse des prix de la plupart des minéraux et des métaux)
— Réduire la dépendance à un approvisionnement permanent de ressources essentielles provenant de pays politiquement instables
— Soutenir les initiatives, résolutions et actions légales des Nations Unies, de l’Union européenne, de l’OCDE et des gouvernements nationaux pour la préservation des ressources nationales et de l’énergie, tout en améliorant la protection de l’environnement
Ainsi, la récupération des ECs contenant des CRMs, tels que les condensateurs électrolytiques au tantale, représente un objectif conséquent.

### 3.4.4 Focus sur des ECs ciblés

La littérature sur l’impact de la récupération d’EC est très limitée. Des études sur les condensateurs ont pu être faites, mais ce n’est pas le cas pour la plupart des ECs. Ainsi, le tableau 6 ci-dessous recense les informations connues sur les ECs les plus répandus afin d’avoir une idée générale de l’attractivité que peut représenter la récupération de différents ECs.

Composant | Métaux précieux/
rares

Impact environnemental Impact économique

Circuits intégrés (IC) Or, cuivre, terres rares Fabrication complexe, forte consommation d’énergie, production de déchets toxiques

Récupération rentable, nécessite tests fonctionnels. Remise à neuf pertinente en cas de crise d’approvisionnement
Capacités (condensateurs)

Aluminium, tantale
(métal critique)
Extraction | du | tan-
tale | problématique
(éthique/environnement),
zones de conflit

Valeur dépendant du matériau. Très prisé en cas de pénurie (ex. crise COVID)

Inductances | Cuivre (en grande
quantité), | parfois
ferrite

Production énergivore (fusion, traitement thermique)

Le cuivre a un prix de base élevé, récupération intéressante
Transistors | Silicium, germanium,
parfois arsenic/gallium

Processus de fabrication hightech, énergivore, production de déchets toxiques

Certains modèles (puissance/spécifiques) ont une forte valeur de revente
Résistances | Cuivre, étain, carbone,
parfois matériaux fins
exotiques

Faible impact individuel, mais significatif à grande échelle (production de masse)

Faible valeur unitaire, mais récupération possible en grande quantité

Table 6 – Comparatif des ECs selon leur composition, impact environnemental et économique

Au vu des informations que j’ai pu trouver et que je recense dans le tableau 6, nous pouvons voir que les ECs intégrés sont les parfaits candidats pour la récupération. En effet, par leur intérêt économique, leur durée de vie, mais également leur impact environnemental, ils remplissent toutes les cases pour susciter notre intérêt à la récupération. Néanmoins, ils peuvent se révéler difficiles à tester. Dans le cadre du stage, la thématique de test est limitée et ne pourra permettre d’assurer le test de ce type d’EC. Cependant, le laboratoire souhaite également développer cette thématique dans le futur. Ainsi, j’ai fait le choix de récupérer ces ECs, même si, dans l’état, je ne pourrai les tester. L’objectif est de permettre leur récupération afin que le test de ces derniers puisse être étudié par la suite. Afin de tout de même avoir une certaine indication sur l’endommagement des ECs au cours de la récupération, j’ai également choisi de cibler les capacités électrolytiques ou encore au tantale qui représente un intérêt pour l’environnement. Dans certains cas, leur récupération peut également être intéressante économiquement parlant, mais du point de vue de leur durée de vie, les capacités électrolytiques ne sont pas forcément fiables du fait de l’évaporation des gaz les contenants. Néanmoins, le simple fait de la récupérer et d’avoir des informations sur la capacité restante de cette dernière est intéressant et permettra d’avoir plus d’informations sur le potentiel de récupération de ces ECs.

### 3.5 Applications prometteuses

À travers cet état de l’art, différentes applications ont pu être parcourues [11], [24], [28], [13], [33], [10], [8], [12].
Outre ces cas d’études, certaines entreprises se sont également spécialisées dans la récupération d’ECs spécifiques. Retronix favorise, par exemple, la réparation et la réutilisation de BGAs. Cette expertise permet à leurs clients de s’approvisionner en ECs sans être impactés par un facteur lié à une crise ou à une pénurie, etc.[20]
Reuse Component rachète des jeux de WPCB afin de récupérer et de revaloriser les ECs présents sur les cartes. Ils offrent ainsi aux industriels la possibilité de gérer leurs DEEE de manière écoresponsable tout en créant un marché de revalorisation des ECs de seconde vie. Leur démarche de récupération implique de s’adapter à chaque carte. Ainsi, un nombre minimal de cartes identiques est nécessaire afin de rentabiliser la démarche.

### 3.6 Conclusion État de l’art

La récupération d’ECs est une démarche prometteuse pour réduire les impacts environnementaux des DEEE. Malgré certaines contraintes techniques, les perspectives sont nombreuses.
Néanmoins, l’analyse de la littérature met en évidence plusieurs points clés [25] :
— L’absence d’acteurs clairement identifiés dans les filières de démontage, ainsi que le manque d’études traitant de la réparabilité, du remanufacturage et du reconditionnement
— La difficulté de mettre en œuvre la réutilisation, principalement à cause des incertitudes liées à la fiabilité des ECs et à la complexité du processus de démontage
— L’importance d’intégrer les principes de circularité dans les exigences d’éco-conception, ainsi que la nécessité de réaliser une analyse de cycle de vie (ACV) complète du produit
— Le besoin global de repenser le modèle économique actuel
Ainsi, dans les années à venir, une mobilisation plus importante autour de la gestion des DEEE, devenue un enjeu croissant, sera essentielle afin de combler les manquements actuels.
À l’échelle du stage, cet état de l’art m’a permis d’obtenir une vision globale des problématiques liées aux DEEE. Par ailleurs, j’ai pu explorer les différentes initiatives déjà engagées en matière de systèmes automatisés pour la récupération des ECs. Nous pouvons cependant relever le peu d’informations détaillées pour les différents systèmes mis en place. Ce manque d’informations a rendu mon étude complexe et m’a demandé des tests supplémentaires afin d’avoir plus d’informations sur l’intégration des différentes solutions. D’un point de vue organisationnel, j’ai fait le choix de recentrer mon travail sur les thématiques de dessoudage et de désassemblage, en ciblant un jeu de cartes électroniques spécifiques et un ensemble d’ECs bien définis. Suite à ce choix, j’ai pu identifier les ECs présentant un intérêt particulier pour la récupération. En somme, les objectifs du stage s’orientent vers la mise en place d’un banc flexible automatisé de récupération d’ECs, dans une optique de revalorisation maximale de ces derniers. Cette démarche pourrait permettre au CEA de réutiliser des ECs récupérés sur des rebuts pour des prototypes. Elle marque aussi un pas vers le développement d’une dynamique autour de la récupération d’ECs. L’objectif pour le laboratoire sera ensuite d’affiner les protocoles de test afin de garantir la fiabilité des ECs récupérés. Ce projet s’inscrit pleinement dans le contexte du marché naissant de la revalorisation des déchets électroniques. D’autre part, l’un des objectifs sera également de rendre le projet open source. À ce jour, il n’existe pas de station de récupération automatisée facilement implémentable. Ainsi, rendre possible l’accès à un outil tel que celui-ci serait intéressant pour les personnes voulant se tourner vers cette dynamique.

## 4 Description des méthodes utilisées

À présent que l’état de l’art a été mené et que les objectifs du stage ont été décrits, nous allons nous intéresser aux différentes méthodes et choix que j’ai faits afin de mener à bien la conception du système automatisé de récupération d’ECs.

### 4.1 Méthode organisationnelle

Pour structurer mon stage, j’ai mis en place un diagramme de GANTT afin d’anticiper les temps d’attente, repérer les points durs et garder un fil conducteur. Tout au long du stage, j’ai contrôlé et ajusté ce diagramme pour suivre mon avancement, détecter d’éventuels retards et, si nécessaire, faire des choix de simplification pour gagner le temps manquant.

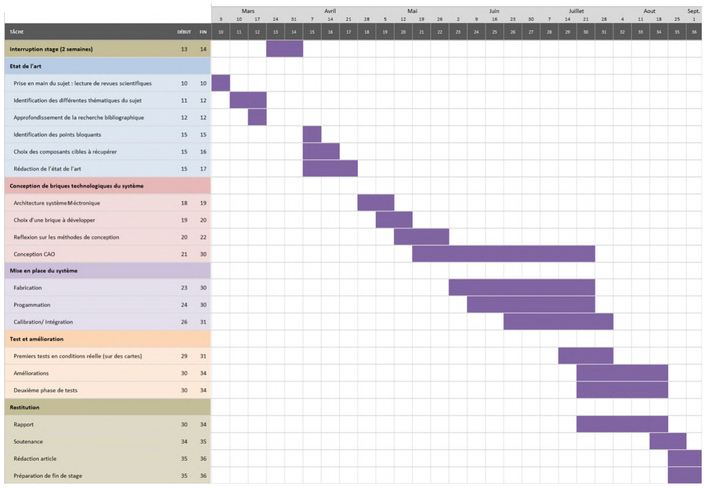
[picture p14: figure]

Figure 8 – Diagramme de GANTT

D’autre part, des points de stage hebdomadaires avec mes tuteurs m’ont permis de régulièrement restructurer mes idées et partager mes avancées avec ces derniers. Cet exercice m’a grandement aidé d’un point de vue organisationnel, mais aussi dans mes réflexions et mes objectifs. En effet, cela m’a permis de prendre du recul de manière régulière et de savoir où j’en étais avec des objectifs clairs.

### 4.2 Cahier des charges / Analyse fonctionnelle simplifiée

Suite à l’état de l’art et aux choix que celui-ci a amené, j’ai pu construire un cahier des charges que l’on peut retrouver ci-dessous table 7. L’objectif ici était de clarifier les fonctions clés que doit remplir la station de récupération.

Fonction | Critère | Importance
Dessoudage permettant le réemploi | Fonte de l’étain en suivant les caractéristiques de tempé-rature utilisé pour le brasage des ECs | 3
Désassemblage | Désolidarisation de l’EC de la carte : la tête de préhen-sion se positionne au-dessus de l’EC, puis procède à son extraction du PCB maintenu en place par un support. | 3
Récupération de l’EC | Dépose de l’EC dans une zone définie | 1
Test de l’EC | Test performant de bonne conformité des ECs | 2
Non endommagement de l’EC à ré-cupérer | Température à ne pas dépasser, courbe de température | 3
Non endommagement des ECs alen-tour | Seuil de température à ne pas dépasser autour de l’EC cible (éviter chauffe à répétition) | 2

Fonction | Critère | Importance
Récupération automatisée de plu-sieurs ECs | Mobilité de la tête de désassemblage en 3D : atteindre différentes positions + connaissance des positions des ECs cibles | 2
Impact environnemental | Impact de récupération < fabrication. Éviter dégagement gazeux, T° < 280°C [34], gestion des gaz | 3
Traiter des PCB variées | taille et forme varié | 3
Structure résistante aux T° | La structure doit résister à des températures pouvant aller jusqu’à 300°C | 3

Table 7 – Cahier des charges fonctionnel

Cette formalisation du besoin m’a ensuite permis d’analyser les fonctions à satisfaire et de faire des choix afin d’avoir des objectifs réalisables et pertinents.
Nous pouvons alors recenser plusieurs fonctions que je vais à présent présenter, accompagnées des solutions fonctionnelles associées.

— Désassemblage : la solution retenue avec l’état de l’art est l’aspiration. La force d’aspiration doit être suffisante pour avoir un retrait de l’EC. Cette dernière et lié à l’aspiration générer par la station mais également par le diamètre de la ventouse. Afin d’y parvenir, il est nécessaire d’avoir en plus de l’aspiration un effet de succion combiné à un effort dans le sens du retrait. Pour y parvenir, il est possible d’utiliser un pad flexible pouvant être assimilé à une ventouse lorsqu’elle est combinée à une aspiration. En complément, il faut également appliquer une force de retrait verticale, vers le haut. Par ce choix de solution, je me dirige alors vers un retrait en série identifiable comme un pick & place inversé.
Combiné à cette fonctionnalité, il est aussi nécessaire de connaître les ECs ciblés. Au vu du temps à ma disposition, mais aussi du champ de technicité du laboratoire, je n’ai pas fait le choix de m’orienter vers de la vision. La solution choisie est de se servir des fichiers de fabrication, qui donnent des informations sur la position des ECs par rapport à un point de la carte. Avec ces informations, il est alors possible de référencer le premier EC à récupérer par rapport à la référence de notre système et d’en déduire la position des autres ECs à condition que les axes de la machine soient alignés avec ceux du PCB.
— Automatisation : L’objectif de la station de récupération est de pouvoir récupérer plusieurs ECs sans intervention de l’utilisateur entre le premier EC récupéré et le dernier. Le choix que j’ai fait pour le désassemblage conditionne ainsi grandement l’automatisation du fait que l’on s’oriente vers un retrait en série. Ainsi, mon système doit être capable de se déplacer en x et y pour permettre la récupération et la dépose de différents ECs, et également en z pour, entre autres, assurer la force de retrait nécessaire au désassemblage des ECs ainsi que l’évitement des autres ECs lors du déplacement de la tête. La solution que j’ai choisie a alors été d’utiliser la structure d’une imprimante 3D obsolète.
— Dessoudage : suivi de la courbe de température utilisée pour le brasage des ECs.

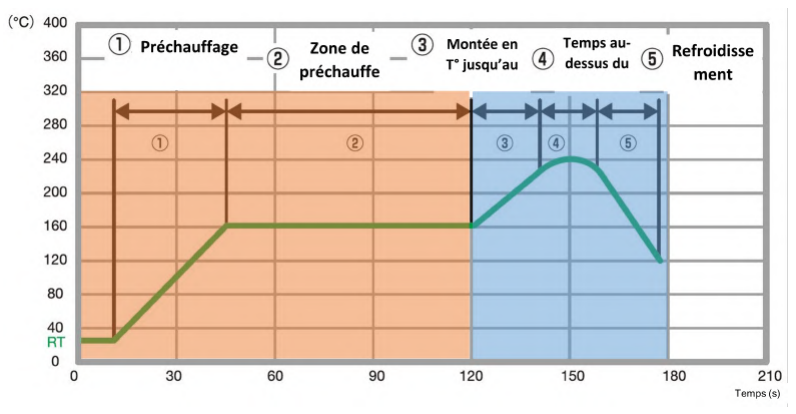
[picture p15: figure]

Figure 9 – Courbe de température dessoudage

On peut alors dénombrer deux zones clés, le préchauffage avec son plateau (en orange sur la courbe) ainsi que le chauffage avec lequel l’on atteint la température de fusion du brasage (en bleu sur la courbe). D’après la littérature, la température de préchauffe varie entre 150°C et 200°C tandis que la température de chauffage varie entre 250°C et 260°C (34). Ainsi afin d’homogénéiser la préchauffe et de paralléliser légèrement la récupération, sans pour autant endommager les ECs, j’ai opté vers une solution où l’on vient préchauffer l’entièreté de la carte aux alentours de 125°C puis chauffer localement une zone avec une autre source de chaleur afin de suivre la deuxième partie de la courbe de température qui atteint une température aux environs de 255°C. Les ECs de cette zone sont alors récupérés sans avoir à effectuer tout le cycle. Une fois les ECs de la zone récupérés, on peut passer à la zone suivante et réitérer uniquement le cycle de chauffe. Au vu des solutions de chauffe étudiées dans l’état de l’art, j’ai fait le choix d’utiliser une plaque IR pour assurer un préchauffage homogène de la carte et un pistolet à air chaud pour assurer un chauffage localisé à haute température facilement contrôlable afin de suivre la courbe de température précise de la zone correspondante.

Les différentes fonctionnalités clé ainsi que les solutions associées sont résumées ci-dessous (figure 10).

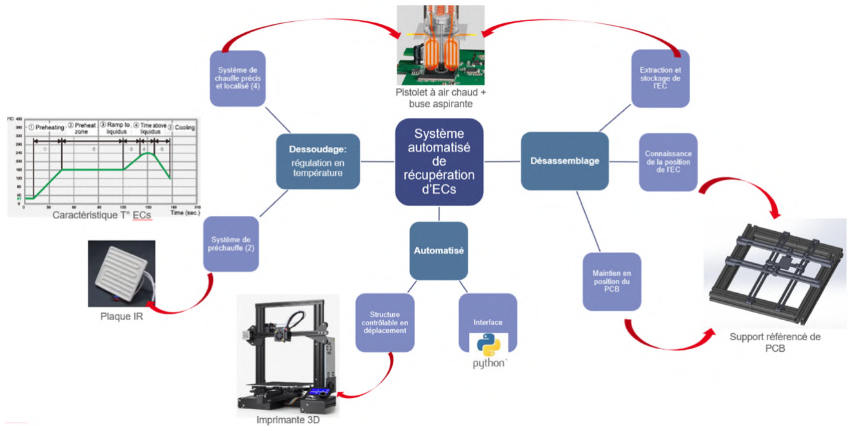
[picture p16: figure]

Figure 10 – Schéma fonctionnel

En utilisant une approche basée sur des fonctions à remplir, j’ai pu avancer de manière méthodique afin de trouver des solutions avec ce que j’avais à disposition dans le laboratoire et également avec ce que je pouvais trouver sur le marché.

— Plaque IR : chauffage homogène, difficile de réguler précisément la température due à l’inertie, mais ce n’est pas problématique pour la fonction à remplir où l’homogénéité est la plus importante. Le choix de la plaque a été pris en considérant l’encombrement, le coût financier ainsi que les caractéristiques techniques en termes de capacité de chauffe.
— Pistolet à air chaud combiné à la buse aspirante (que l’on nommera "pistolet" par commodité) : le gros avantage de cette brique fonctionnelle est qu’elle assure la fonction de désassemblage et de dessoudage localisé à haute température. Ainsi, le contrôle de cet unique élément me permettra de chauffer la zone de l’EC ciblé tout en assurant son désassemblage avec un seul contrôle en position.

— Le support de carte : conçu sur mesure en s’inspirant des supports existants. Les contraintes étaient sur la taille du système et la fonctionnalité permettant la tenue de cartes variées.

— L’interface Python : permettre le contrôle de la station de récupération en venant commander l’imprimante ainsi que les différents éléments de chauffe tout en assurant l’interface homme-machine

— Imprimante 3D : possibilité de commander l’imprimante 3D par simple commande Gcode via un port série pour assurer la communication avec l’interface Python. L’objectif est alors de positionner le pistolet sur le support où était à l’origine fixée la tête d’impression initialement prévue pour l’impression 3D et dont il est possible de commander son positionnement.

### 4.3 Méthodes de conception

Une fois les choix fonctionnels faits, j’ai pu commencer la conception de mes différentes briques fonctionnelles ainsi que les éléments permettant leur intégration. Pour chaque élément, la méthode utilisée a été, dans un premier temps, d’identifier les fonctions et les contraintes que doivent avoir mon élément. Dans un second temps, j’ai procédé en me renseignant sur les possibilités existantes afin de remplir les différentes fonctions identifiées en amont. Pour cette deuxième étape, j’ai réalisé des recherches dans la littérature, mais également auprès de collègues du laboratoire pour confronter mes idées et les améliorer. Dans un troisième temps, j’ai regroupé mes idées sur papier en dessinant dans le but d’avoir une meilleure visualisation de la solution envisagée et d’anticiper les problématiques qui pourraient apparaître. Une fois convaincue par la solution, un quatrième temps était consacré à la conception sous SolidWorks. Dans cette étape, j’ai pris garde à réaliser les assemblages dans leur entièreté afin d’anticiper les problèmes liés au montage des vis ou des interférences que je n’avais pas envisagées en amont. Une fois le modèle validé en termes de fonction, je me suis préoccupée dans un second temps des contraintes de fabrication. J’ai par exemple réalisé des pièces par fraiseuse à commande numérique, ce qui m’a emmené vers une conception restreinte par les possibilités offertes par la fraiseuse. Le choix du plan de positionnement de la pièce était alors primordial. Un travail sur les angles intérieurs fonctionnels qui nécessitent d’être vifs a du être réalisé en incorporant une contre-dépouille par exemple.

## 5 Description des réalisations

Afin de réaliser mon système de récupération, j’ai dû concevoir et fabriquer des éléments fonctionnels et des éléments d’intégration. J’ai également dû mettre en place une interface Python permettant de faire l’interface homme-machine et le contrôle des différents éléments. L’intégration des différents thermocouples permettant de mesurer la température en différents endroits ou encore la commande de la station d’air chaud et d’aspiration a nécessité différentes réalisations que nous allons à présent détailler.

### 5.1 Conception et fabrication

### 5.1.1 Support de carte

La première réalisation que j’ai pu faire après mon état de l’art a été le support de carte. L’objectif principal de ce dernier est de maintenir en position une carte électronique quelles que soient sa forme et sa taille (dans une certaine plage). En d’autres termes, pouvoir prendre en charge des cartes qui ne soient pas uniquement rectangulaires.
En termes de contraintes, nous recensons principalement les contraintes liées à la taille et à la température. La contrainte de taille est directement liée à la taille de l’imprimante 3D. Cette dernière possède un plateau sur lequel je voudrais venir fixer le support de carte. Ce plateau se déplace selon l’axe y et induit une contrainte de taille due à la structure de l’imprimante l’environnant. Ainsi, le support de carte doit être inférieur à 250mm x 250mm en largeur et en profondeur (voir figure 11). Au niveau de la hauteur, nous n’avons pas de contrainte forte, ainsi ce n’est pas notre préoccupation phare.

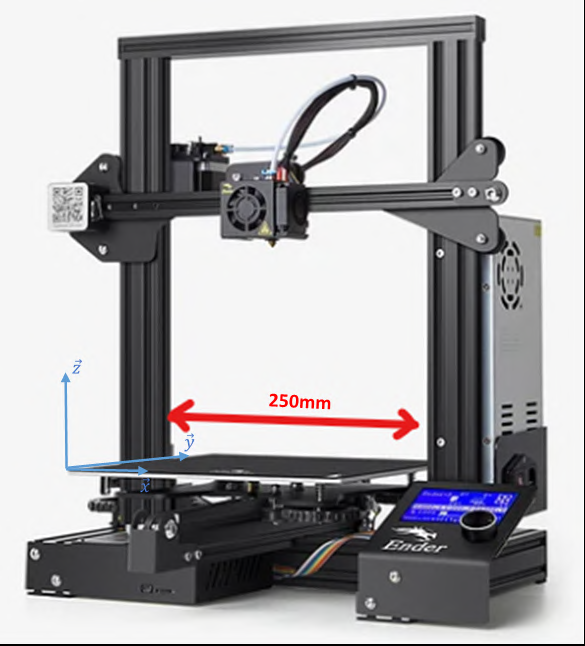
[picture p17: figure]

Figure 11 – Imprimante Ender 3

En termes de température, la structure doit pouvoir résister à des températures pouvant atteindre les 300°C. Cette contrainte a ainsi eu un effet direct sur le choix du matériau et par suite sur la conception et la fabrication. La structure ne sera pas soumise à d’autres contraintes que la température, ainsi, je me suis orienté vers de l’aluminium.

•Conception
Le système est constitué de quatre profilés assurant la translation de quatre bras. Sur ces quatre bras sont positionnés des supports visant à maintenir la carte par compression entre ces supports et la carte en venant serrer les bras sur lesquels ils sont positionnés. L’image 12 illustre le système.

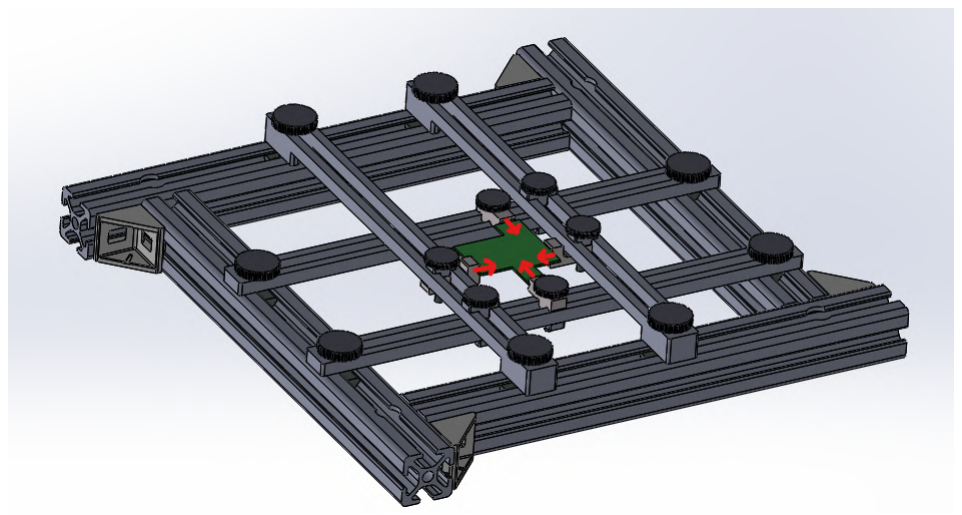
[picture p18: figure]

Figure 12 – Support carte

•Intégration du pistolet à air chaud et à aspiration
L’intégration du système est assez simple. En effet, quatre trous se situant dans les quatre coins de la plaque mobile existante nous permettent de venir fixer le système à cette dernière.

•Fabrication
Étant donné que le matériau que j’ai sélectionné est l’aluminium, il est nécessaire d’usiner les différents éléments. On dénombre alors les quatre barres ainsi que les petits supports. Les profilés ont eux été récupérés d’un ancien projet. Pour l’usinage, je me suis orienté vers une fabrication alliant une fraiseuse à commande numérique et une fraiseuse conventionnelle pour les trous ne pouvant être réalisés par la première méthode au vu de la surface d’usinage choisie. Ainsi, une réflexion sur la surface d’usinage a dû être faite. L’identification des surfaces utiles m’a alors permis de faire ce choix. Nous pouvons retrouver ces dernières en bleu sur l’image 13. La surface d’usinage pour cette pièce est celle sur laquelle repose la pièce sur l’image 13.
D’autre part, le choix de la fraise au vu de l’épaisseur de la pièce devait être d’au moins 2mm du fait de la longueur utile de coupe de la fraise. Cette caractéristique a un impact direct sur les congés intérieurs usinables. En effet, ces derniers doivent avoir un rayon supérieur ou égal à celui de la fraise. Cette contrainte est problématique lorsque l’on souhaite avoir des coins à 90° ce qui était mon cas. Afin de pallier cela, j’ai rajouté des contre-dépouilles dans ces zones critiques. Le support de carte fabriqué est alors visible figure 14.

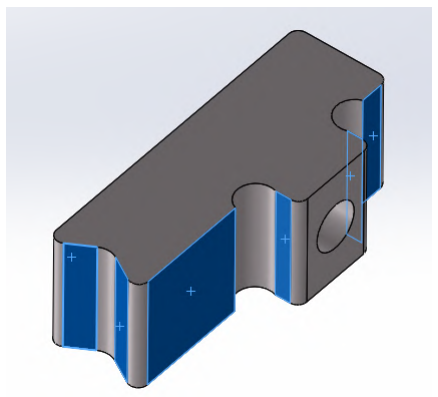
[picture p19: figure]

Figure 13 – Pièce support carte

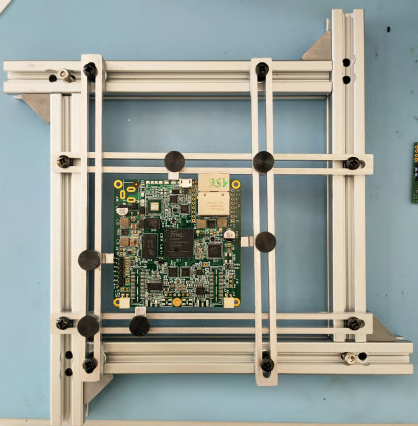
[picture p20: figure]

Figure 14 – Support carte conçu et

fabriqué

### 5.1.2 Support plaque IR

Afin d’assurer l’intégration de la plaque IR sur l’imprimante, j’ai réalisé un support permettant de fixer l’ensemble sur la plaque mobile de l’imprimante. À nouveau, j’ai réutilisé des trous de vis déjà existants pour fixer le système.

•Conception
Le support devant simplement servir d’interface de fixation, sa conception s’est révélée assez basique. Le gros de la réflexion n’a pas été fait au regard des contraintes fonctionnelles, mais au regard de la fabrication. L’objectif était principalement de trouver une conception permettant de faciliter au mieux la fabrication. J’ai donc fini par choisir une solution composée de deux plaques liées par des entretoises. Cette solution est visible sur la figure 15. La pièce en accordéon observable dans l’assemblage était fournie avec la plaque IR lors de l’achat.

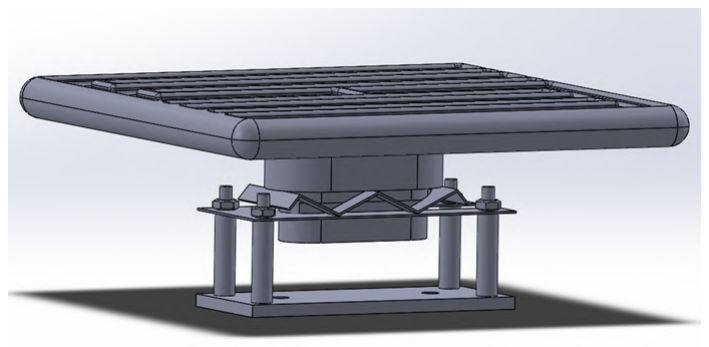
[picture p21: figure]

Figure 15 – Support plaque IR

•Fabrication
Grâce aux choix de conception que j’ai pu faire, la fabrication s’est limitée à la découpe de deux plaques en aluminium que j’ai pu faire à l’aide d’une scie à métaux et d’une d’une fraiseuse conventionnelle pour effectuer les différents trous. Le système intégré sur l’imprimante 3D est visible sur l’image 16

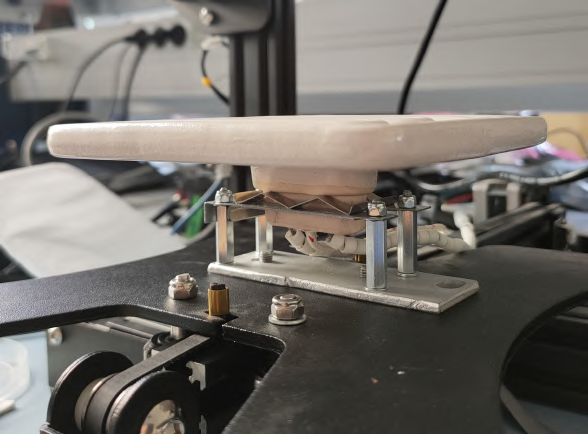
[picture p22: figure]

Figure 16 – Support plaque IR fabriqué

### 5.1.3 Intégration du pistolet

Le dernier élément à intégrer parmi les différentes briques fonctionnelles est le pistolet. L’intégration de ce dernier s’est révélée la plus complexe de par les fonctionnalités que je recherche.
Le pistolet doit être fixé sur le support qui était à l’origine utilisé pour fixer la tête d’impression. Ce support est lui-même commandable en position selon l’axe ⃗x et ⃗y. En plus de cela, je souhaite pouvoir récupérer des ECs variés. Et qui dit EC varié, dit également hauteur variée. En effet, une capacité électrolytique sera bien plus haute qu’un composant intégré. Pour pallier cette contrainte, ma solution, illustré sur la figure 17, est de permettre une translation du pistolet selon l’axe ⃗z. L’objectif étant que lorsque le pistolet n’est pas en contact avec un EC (position repos), il repose sur une butée. Puis, lorsque le pistolet rentre en contact avec un EC, grâce à une translation selon z du support de tête d’impression, le pistolet viendra reposer sur ce dernier alors que le support continuera lui sa descente vers une hauteur correspondant au supposé contact du pistolet avec la carte électronique. Ceci est rendu possible par une liaison glissière entre le support et le pistolet. Grâce à un capteur de fin de course, qui détecte lorsque le pistolet ne repose plus sur la butée, je serai en capacité de déduire la hauteur à laquelle le pistolet est rentré en contact avec l’EC. Cela nous permettra d’y revenir par la suite et de soulager la carte du poids influé par la masse du pistolet.

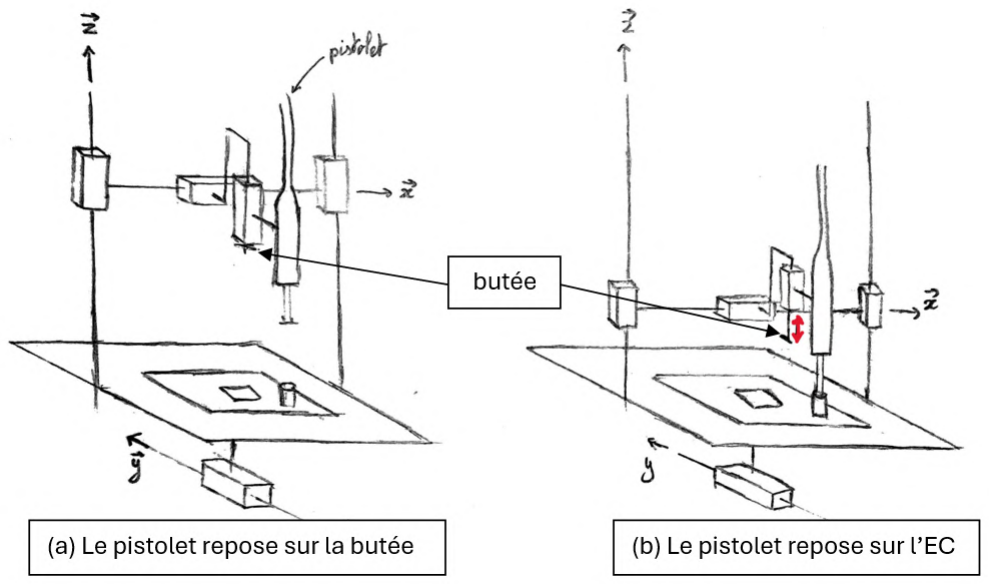
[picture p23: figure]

Figure 17 – Système de récupération non contraint en hauteur d’EC

D’autre part, le pistolet est équipé d’un système de ressort permettant le désassemblage de l’EC cible une fois celui-ci dessoudé. Ce phénomène est rendu possible lorsque la force d’aspiration F⃗A est supérieure à la force du ressort. Concrètement, l’aspiration est mise en route, générant F⃗A ; le pistolet remonte alors, contraignant le ressort, qui développe une force F⃗R telle que F⃗R < F⃗A. Cette relation décrit le fait que la buse du pistolet reste accrochée à l’EC malgré le fait que le pistolet remonte en générant une force contraire à F⃗A en permettant le chargement du ressort afin d’avoir une force d’extraction globale inférieure à F⃗A. Au début du dessoudage, la force liée à la brasure F⃗B est supérieure à F⃗R. Lorsque la brasure passe à l’état liquide, la relation devient F⃗A > F⃗R > F⃗B, ce qui permet le désassemblage de l’EC. La figure 18 illustre ce concept.

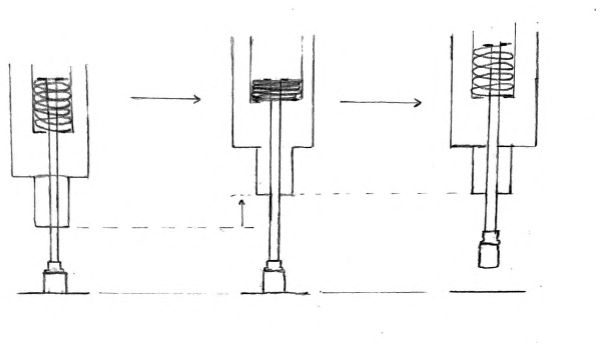
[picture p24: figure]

Figure 18 – Fonctionnement du désassemblage

La solution pour assurer le désassemblage est alors présentée en étapes :
— Positionner le pistolet au-dessus de l’EC à récupérer.
— Translater selon −Z⃗ pour atteindre la hauteur correspondant au contact du pistolet avec la carte électronique dans le cas où il n’y a pas d’EC s’interposant (= hauteur min d’un EC).

— Retrouver la hauteur h de l’EC cible à l’aide du capteur de fin de course (étant donné que la surface supérieure de l’EC aura une position selon z supérieure à celle de la carte, le déplacement du pistolet dans sa glissière aura déclenché l’activation du capteur de fin de course).

— Commencer le cycle de chauffe de dessoudage avec la mise en route de l’aspiration.
— Déplacement selon Z⃗ en h + δ. δ étant la translation supplémentaire pour charger le ressort.

— Désassemblage par relâchement du ressort une fois la brasure fondue.

•Conception
Notre objectif en termes de conception est d’assurer une liaison glissière selon ⃗z entre le pistolet à air chaud et le support (anciennement de la tête d’impression de l’imprimante 3D). S’ajoute à cela l’intégration du capteur de fin de course.
Afin d’assurer la liaison glissière, la solution technologique retenue est l’utilisation d’un guidage linéaire composé d’un rail prismatique et d’un patin. Le rail est alors en liaison encastrement avec le support de tête d’impression, tout comme le patin avec le pistolet. En somme, deux éléments sont nécessaires dans le but d’assurer ces liaisons.

Éléments de liaison entre le support de la tête d’impression et le rail : Afin d’assurer cette liaison, la pièce doit d’une part se fixer sur le support et d’autre part sur le rail. En utilisant les trous déjà présents sur le support et le rail, j’ai pu concevoir la pièce voulue tout en essayant de limiter les efforts générés dans la pièce.

Éléments de liaison entre le patin et le pistolet : Le patin présente une surface plane avec quatre trous de fixation taraudés que j’ai mis à profit pour fixer l’élément de liaison au patin. La difficulté pour cette liaison se trouve avec le pistolet. Ce dernier est un cylindre non régulier, ce qui complique la conception. On recense également une gorge. Ainsi, la pièce conçue intègre un collet en demi-sphère permettant d’y caler la gorge du pistolet. Avec cette solution, nous avons à ce stade une liaison rotule. Afin de supprimer ces degrés de liberté tout en permettant d’ajuster l’inclinaison du pistolet par rapport au rail et en s’adaptant à la non cylindricité du pistolet, j’ai opté pour une pièce en deux parties avec quatre serrages distincts. De plus, l’intégration de trois vis positionnées à 120° le plus éloignées possible de la liaison rotule me permet d’ajuster finement l’inclinaison afin de s’assurer que le pistolet soit bien parallèle au rail et par suite limiter les efforts. La solution est visualisable image 19.

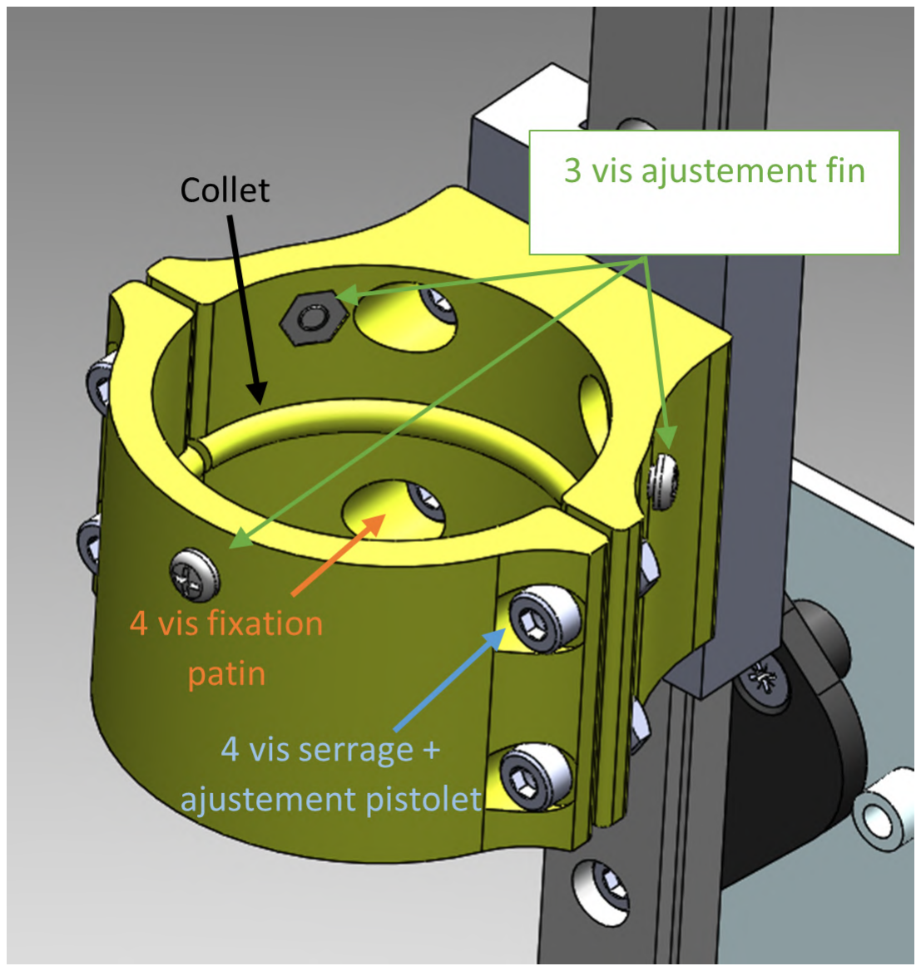
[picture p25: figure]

Figure 19 – Éléments de liaison entre le patin et le pistolet

Élément de fixation du capteur de fin de course : Le capteur de fin de course doit donner des informations sur la position du pistolet par rapport à la butée. En somme, le problème revient donc à déduire la position du patin. La pièce venant intégrer le capteur peut alors être positionnée sur le rail avec pour objectif de détecter les mouvements du patin. Afin que le capteur ne soit pas en continu soumis au poids du pistolet, celui-ci est positionné tangent au mouvement du patin. Ainsi, un ajustement précis est nécessaire afin que le patin soit suffisamment proche du capteur pour le déclencher sans pour autant être trop proche et bloquer son mouvement. Ainsi, l’ajustement de la position est rendu possible par des trous oblongs.

Les différents éléments de la conception du support sont illustrés sur l’image 20 ci-dessous.

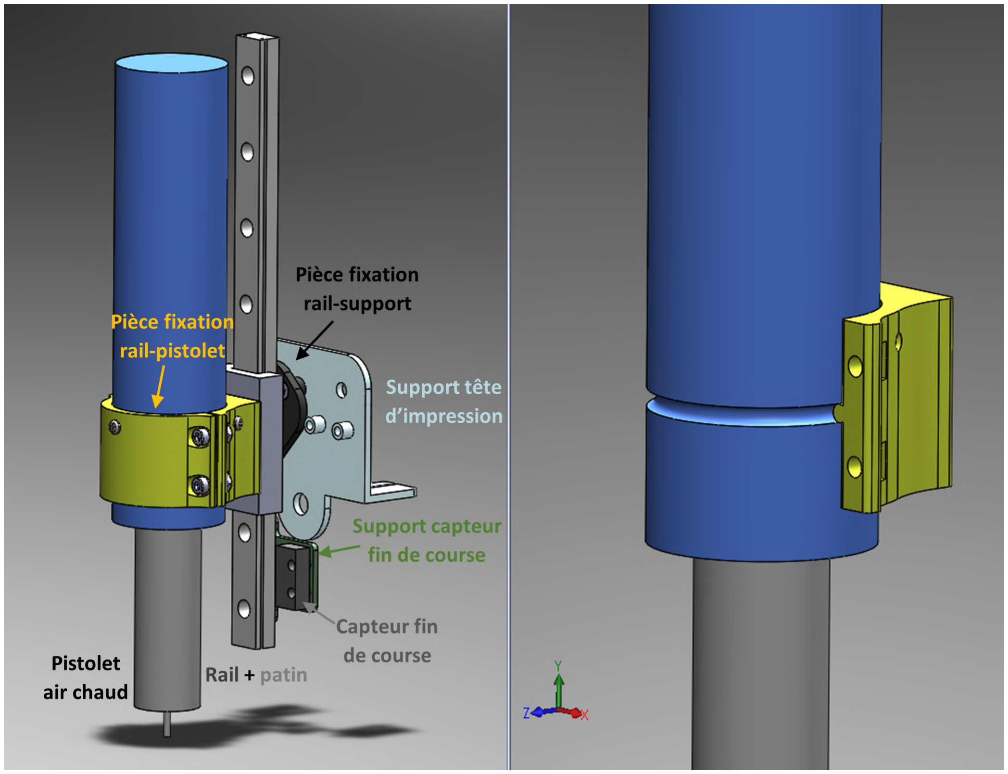
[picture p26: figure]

Figure 20 – Éléments d’intégration du pistolet

•Fabrication

Éléments de liaison entre le support de la tête d’impression et le rail : pour la fabrication, la pièce ne sera pas exposée à des températures critiques, ainsi j’ai pu m’orienter sur l’impression 3D. Le choix du type de filament a lui été induit par les efforts qui seront appliqués sur la pièce. Afin d’éviter des déformations, j’ai utilisé du PLA renforcé en fibres de carbone.

Éléments de liaison entre le patin et le pistolet : Cet élément est lui davantage exposé à la température. Néanmoins, cette dernière nous permet tout de même d’utiliser l’impression 3D, mais cette fois en utilisant du filament ASA. Ce dernier à une résistance thermique allant jusqu’à 93°C contre 50°C pour le PLA. La pièce sera exposé à une température qui ne devrait pas dépasser les 90°C mais s’en approchant, ainsi, il correspond à notre besoin dans notre cas d’étude.

Élément de fixation du capteur de fin de course Ce dernier élément n’est pas soumis à des efforts importants mais à des température équivalent à la pièce précédente. Ainsi, je me suis à nouveau tourné vers l’impression 3D en utilisant de l’ASA comme filament.

Le système fabriqué et intégré sur l’imprimante 3D est présenté sur l’image 21 ci-dessous.

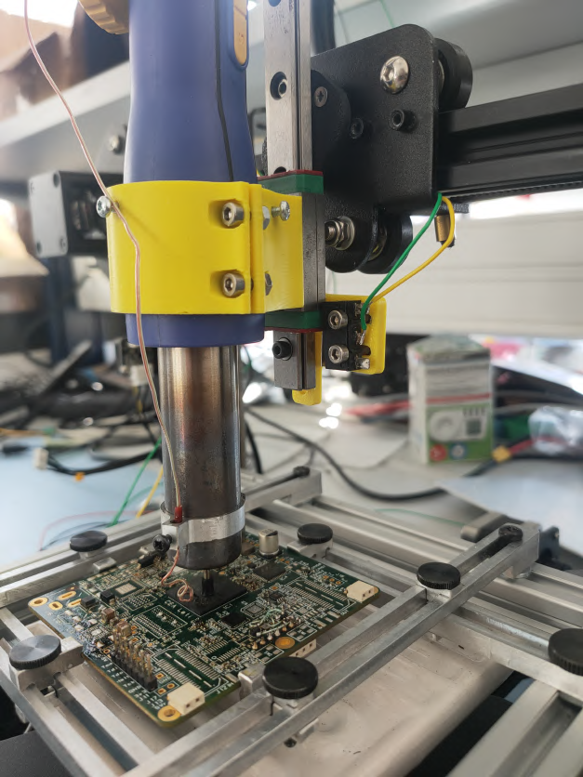
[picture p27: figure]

Figure 21 – Intégration du pistolet

### 5.2 Intégration des thermocouples
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

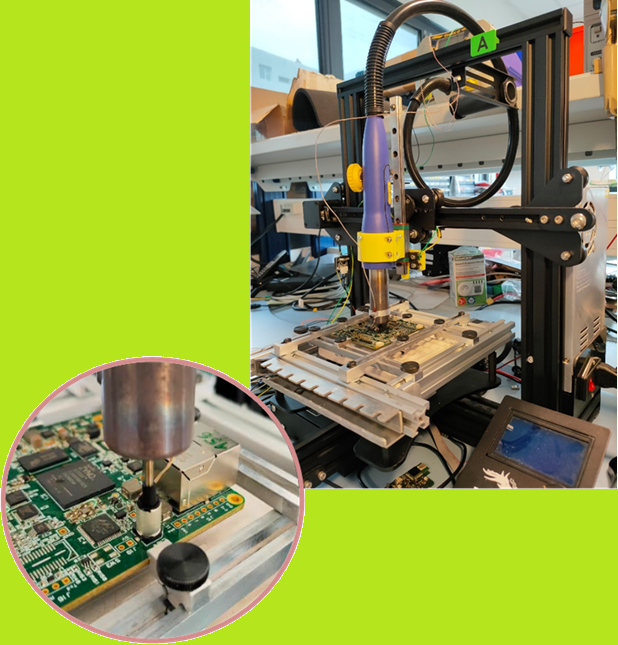
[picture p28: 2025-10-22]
images/Pick&Remove4Reuse.png

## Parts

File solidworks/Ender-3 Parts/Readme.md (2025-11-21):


# Ender-3
The Creality3D Ender-3, a fully Open Source 3D printer perfect for new users on a budget.

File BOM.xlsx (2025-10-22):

N° | Reference | Description | Quantity | Website, provider
1 | Creality ender 3 | open source Creality ender 3 3D printer | 1 | https://www.creality.com/fr/products/ender-3-3d-printer
2 | IR heating System |  | 1
2.1 | IR lamp 120 x 120 mm | IR lamp for BGA rework station - 600W 110V/220v | 1
2.2 | MH1210A 12V | Temperature regulator - 12V | 1
2.3 | support_plaqueIR_v3 | 70 mm x 30 mm fixation | 1 | custom - machined - Aluminium
2.4 | entretoise_m3_20 | entretoise M3 x 20 | 4 | https://fr.rs-online.com/web/p/entretoises-filetees/0221162?gb=s
2.5 | plaquette_substitution_4t | IR lampp fixation part 1 | 1 | custom - machined - Aluminium
2.6 | plaquette_dent_de_scie | IR lamp fixation part 2 | 1 | Delivered with IR Lamp
2.7 | ecrou_m3 | ecrou M3 | 4 | https://fr.rs-online.com/web/p/ecrous-hexagonaux/1224400?gb=s
3 | Hot air soldering system |  | 1
3.1 | HAKKO FR-811 | Hot air soldering station | 1 | https://www.hakko.com/english/products/hakko_fr811.html
3.2 | Arduino MEGA 256 | Arduino MEGA 256 | 1
3.3 | SCHRACK RTS3L005 | Relay | 1
3.4 | plaque_fixation_support | Fixation of the head printer | 1 | already on the 3D printer
3.5 | support_rail | fixaton of the rail | 1 | custom - 3D printed
3.6 | rail | prysmatic rail | 1
3.7 | patin | prysmatic rail Shoe | 1
3.8 | support_2parties_partFixed_v2 | Custom fixation for the hot air gun | 1 | custom - 3D printed
3.9 | support_2parties_partAdd_v2 | Custom fixation for the hot air gun | 1 | custom - 3D printed
3.10 | vis_6pans_m3_12 | M3_12 screw | 10
3.11 | vis_m3_fraise_10 | M3_10 screw | 2
3.12 | ecrou_m3 | M3 nut | 6
3.13 | piece_fin_course | fixation of the limit switch | 1 | custom - 3D printed
3.14 | capteur_fin_course | limit switch | 1
3.15 | ecrou_2-5 | M2 Nut | 4
3.16 | CSPPN-ST-M2_5 | M2_5 screw | 6
3.17 | bague_thermocouple | custom fixation for the thermocouple | 1 | custom - machined - Aluminium
3 | PCB holder |  | 1
3.1 | profile_20_20 | 20 x 20 Aluminium profile | 4 | https://fr.rs-online.com/web/p/tubes-et-profiles-de-structures/2647854
3.2 | equerre_profile | 20 mm T-slot bracket | 4
3.3 | plaque_depose_ec | support for recovered Ecs on the side of the PCB holder | 2 | custom - machined - Aluminium
3.4 | Ecrou à rainure en T - 1809108 | nut for T-slot bracket , profile20 mm, L. 12mm, M4 | 8 | https://fr.rs-online.com/web/p/raccords-pour-elements-de-structure/1809103?gb=s
3.5 | rail_mobile_dessous_P | custom part for PCB Holder 1 | 2 | custom - machined - Aluminium
3.6 | rail_mobile_dessus_P | custom part for PCB Holder 2 | 2 | custom - machined - Aluminium
3.7 | piece_up_serrage_rails_mobiles | custom part for PCB Holder 3 | 2 | custom - machined - Aluminium
3.8 | piece_serrage_rails_mobiles | custom part for PCB Holder 4 | 2 | custom - machined - Aluminium
3.9 | pattes_mobiles_bottom_rail_6 | custom part for PCB Holder 5 | 2 | custom - machined - Aluminium
3.10 | piece_up_serrage_patte_rail_mobile | custom part for PCB Holder 6 | 2 | custom - machined - Aluminium
3.11 | piece_serrage_patte_rail_mobile | custom part for PCB Holder 7 | 2 | custom - machined - Aluminium
3.12 | pattes_mobiles_rail | custom part for PCB Holder 8 | 2 | custom - machined - Aluminium
3.13 | vis_moletee | Thumb screws DIN 653-M3-16 | 6
3.14 | vis_moletee_m4 | Thumb screws M4 | 8
3.16 | entretoise | Entretoise 8 mm x 40 mm | 4

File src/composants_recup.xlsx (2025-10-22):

Nom | x | y | pos_x_depot | pos_y_depot
C107 | 19 | 6 | 115 | 35.4
L13 | 25.5 | 6.5
RG2 | 31.5 | 6.5
IC2 | 39.5 | 21.5
IC6 | 26.5 | 23
IC7 | 11.5 | 35
IC3 | 18 | 41.5
IC1 | 35.5 | 37.5
IC11 | 63.5 | 24.5
IC8 | 55 | 35
IC9 | 55 | 42
IC21 | 65.5 | 50.5
RG1 | 27 | 57.5
IC4 | 42.5 | 59.5
C104 | 33.5 | 68

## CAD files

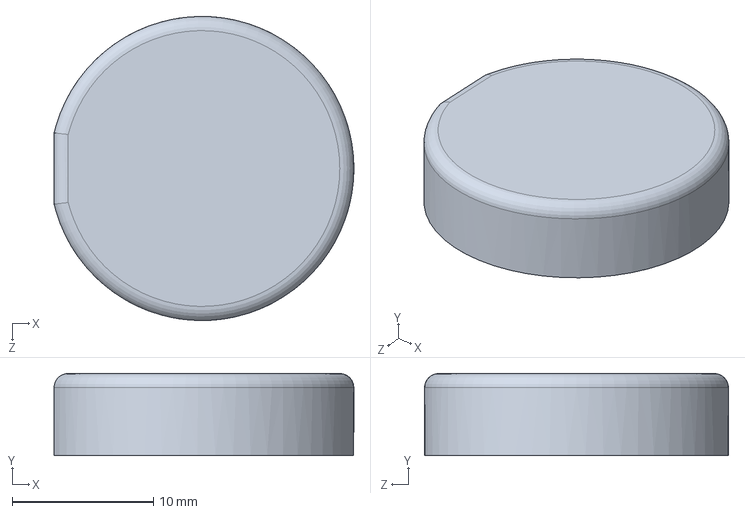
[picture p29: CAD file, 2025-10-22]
solidworks/support_pistolet_air_chaud/axe_maintien.SLDPRT
21.2 x 5.80 x 21.5 mm

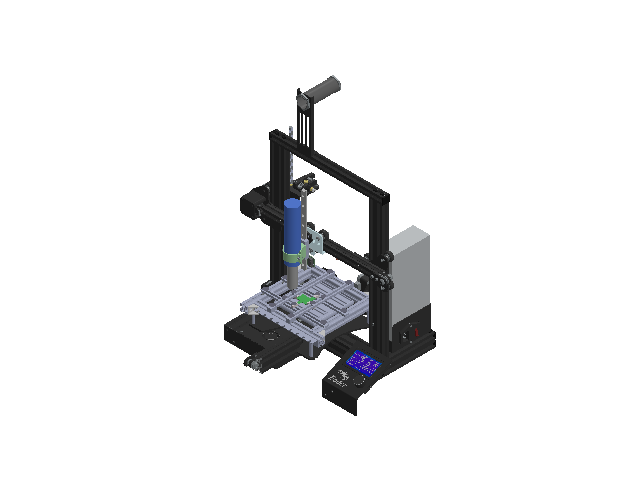
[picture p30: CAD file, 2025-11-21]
solidworks/support_carte_asm_g/asm_general_v3.SLDASM
4040 profile x 2
4040-3 profile
2020-2 profile
2040-3R profile
2040-3L profile
2020 Endcap x 10
M5X45 Socket Head Screw x 14
2020 profile
Z Stent
X motor bracket
42-34 motor x 3
z nut
E motor bracket
X limit switch bracket
X belt
limit switch x 3
2GT-pulley x 2
Copper cover x 4
M4 Split Washer x 5
M3 Split Washer x 2
M4X16 Pan Head Screw x 4
M3X40-P x 4
M3X10 Pan Head Screw x 6
M3X6Pan Head Screw x 18
Rollers x 13
Eccentric column x 5
Spacers for rollers x 11
625pillow x 26
M5 Self-locking nut x 13
624U pillow
M3X18 Socket Head Screw
Extrusion Spring
E gear
E housing 2
E idler tensioner
M3X10 Flush Head Screw x 3
M6 Pneumatic joint
M4X8 Socket Head Screw x 8
X Adjustment Block
M5 T-Slot Nut x 2
M8X25 Pan Head Screw x 2
M8 Self-locking nut x 2
M8 nut x 2
F688 pillow x 4
M5X30 Pan Head Screw x 10
M5 Split Washer
E plate
M5 washer x 3
2040-2 profile
Y belt
Y Motor holder
Y Adjustment Block
M4 T-Slot Nut x 7
Y limit switch bracket
M4X16 Screw x 4
Y plate
Z motor bracket
Z coupler
Z threaded rod
M3X16 Pan Head Screw x 3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

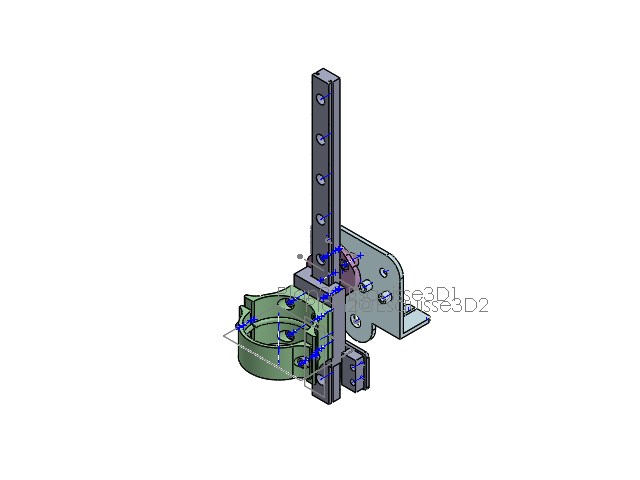
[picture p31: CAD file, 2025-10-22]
solidworks/support_pistolet_air_chaud/asm_integration_pistolet_air_chaud_2.SLDASM
plaque_fixation_support
support_rail
rail
patin
support_2parties_partFixed_v2
support_2parties_partAdd_v2
vis_6pans_m3_12 x 8
vis_m3_fraise_10 x 2
ecrou_m3 x 4
piece_fin_course
capteur_fin_course

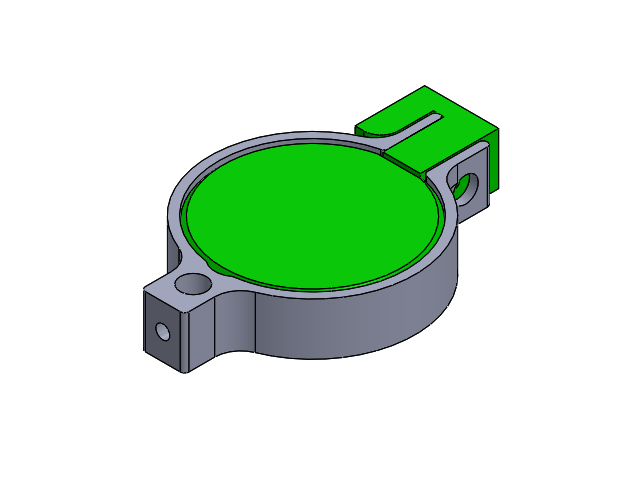
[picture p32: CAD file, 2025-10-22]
solidworks/support_pistolet_air_chaud/asm_bague_piece_percage.SLDASM
bague_thermocouple
aide_percage_bague
250804_axe_maintien

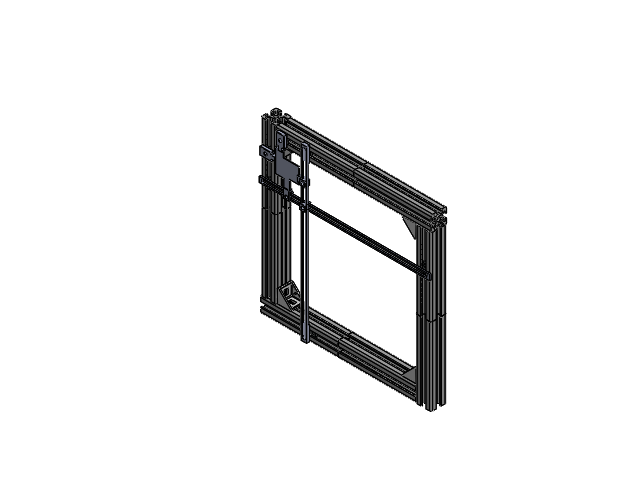
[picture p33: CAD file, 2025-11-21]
solidworks/support_carte_asm_g/asm_test.SLDASM
profile_20_20 x 8
equerre_profile x 4
patte_fixe_v1 x 2
ex_pcb_petit_non_rect
rail_mobile_dessous_P
rail_mobile_dessus_P
piece_serrage_rails_mobiles x 2
pattes_mobiles_rail x 2
piece_serrage_patte_rail_mobile x 2

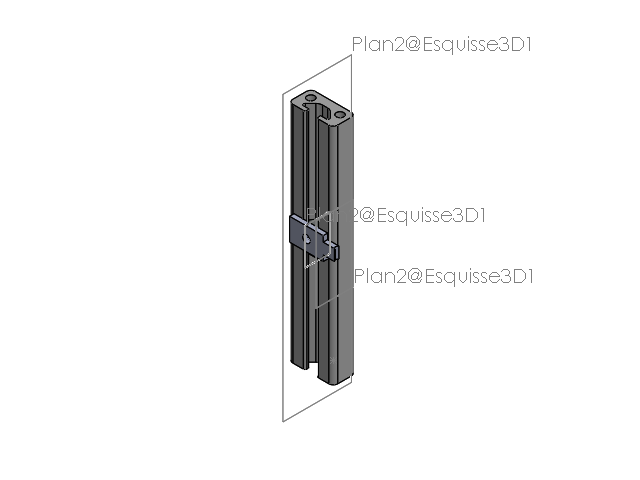
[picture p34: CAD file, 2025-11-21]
solidworks/support_carte_asm_g/Assemblage1.SLDASM
patte_fixe_v1

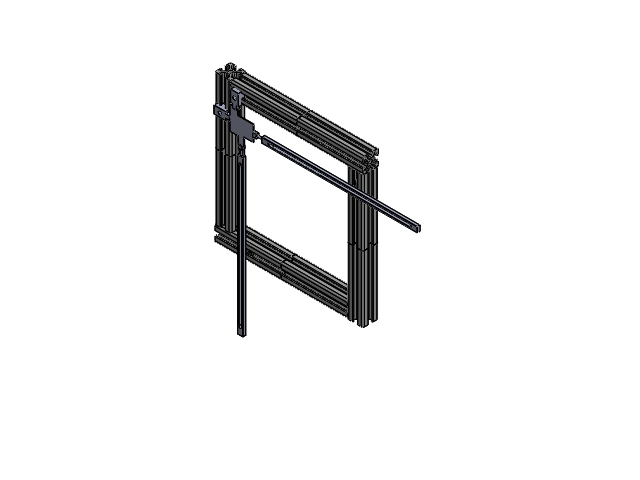
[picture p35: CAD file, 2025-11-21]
solidworks/support_carte_asm_g/asm_socle_pcb.SLDASM
profile_20_20 x 8
patte_fixe_v1 x 2
patte_mobile_bras_v1 x 2
patte_mobile_pince_v1 x 2
ex_pcb_petit_non_rect

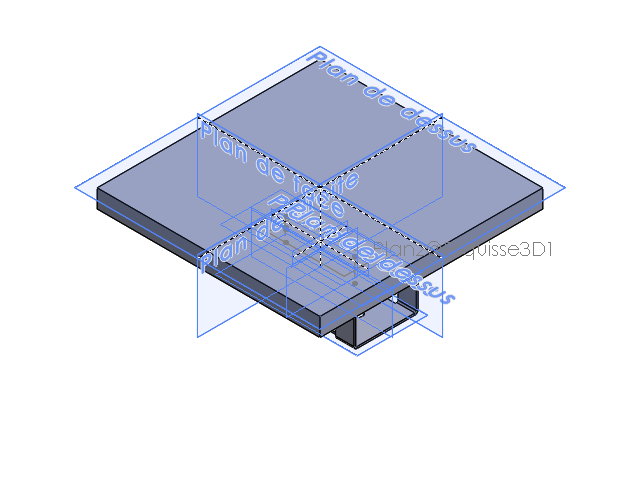
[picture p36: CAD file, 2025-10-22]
solidworks/Support_plaque_IR/asm_support_plaqueIR_v3.SLDASM
support_plaqueIR
plaquette_substitution
plaque_IR
plaquette_dent_de_scie
vis_6pans_m3_6 x 3
ecrou_m3 x 3

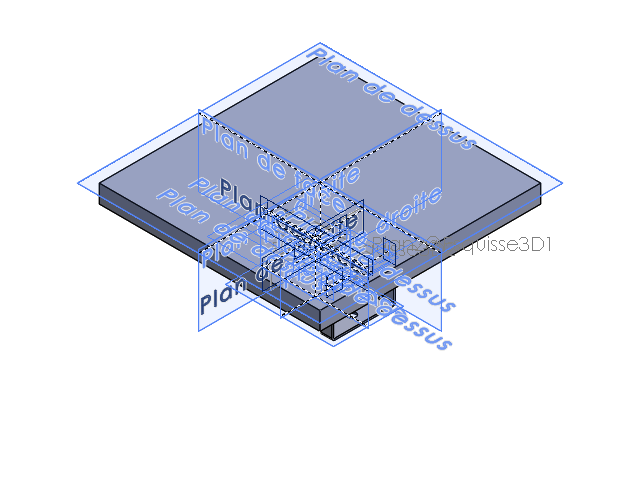
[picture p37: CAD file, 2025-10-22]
solidworks/Support_plaque_IR/asm_support_plaqueIR.SLDASM
support_plaqueIR
pince
fermoire_pince x 2
vis_6pans_m3_6
vis_6pans_m3_12 x 2
plaque_IR
plaquette_serrage
plaquette_dent_de_scie

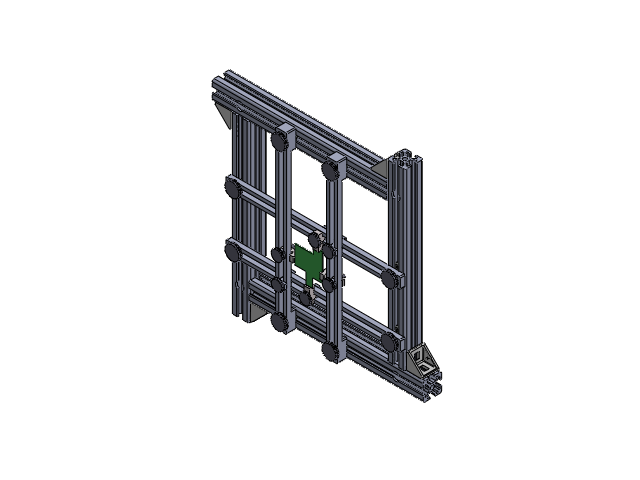
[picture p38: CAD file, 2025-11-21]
solidworks/support_carte_asm_g/asm_socle_pcb_v3.SLDASM
profile_20_20 x 4
equerre_profile x 4
ex_pcb_petit_non_rect
rail_mobile_dessous_P x 2
rail_mobile_dessus_P x 2
piece_up_serrage_rails_mobiles x 2
piece_serrage_rails_mobiles x 2
pattes_mobiles_bottom_rail_6 x 2
piece_up_serrage_patte_rail_mobile x 2
piece_serrage_patte_rail_mobile x 2
pattes_mobiles_rail x 2
vis_moletee.stp x 6
vis_moletee_m4_10.stp x 4
vis_moletee_m4_16.stp x 4

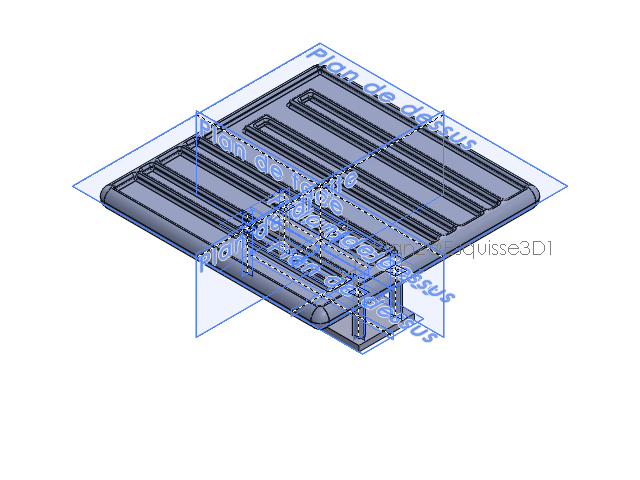
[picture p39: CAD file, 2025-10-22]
solidworks/Support_plaque_IR/asm_support_plaqueIR_vf.SLDASM
support_plaqueIR_v3
entretoise_m3_20 x 4
plaquette_substitution_4t
plaque_IR
plaquette_dent_de_scie
ecrou_m3 x 4

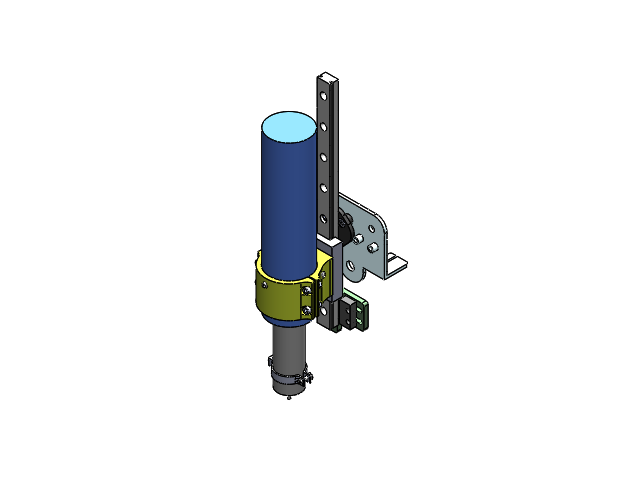
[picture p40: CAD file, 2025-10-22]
solidworks/support_pistolet_air_chaud/asm_integration_pistolet_air_chaud.SLDASM
plaque_fixation_support
support_rail
rail
patin
support_2parties_partFixed_v2
support_2parties_partAdd_v2
vis_6pans_m3_12 x 10
vis_m3_fraise_10 x 2
ecrou_m3 x 6
piece_fin_course
capteur_fin_course
pistolet_air_chaud
ecrou_2-5 x 4
vis_m2-5_4 x 3
bague_thermocouple
vis_m2-5_8
vis_m2_4

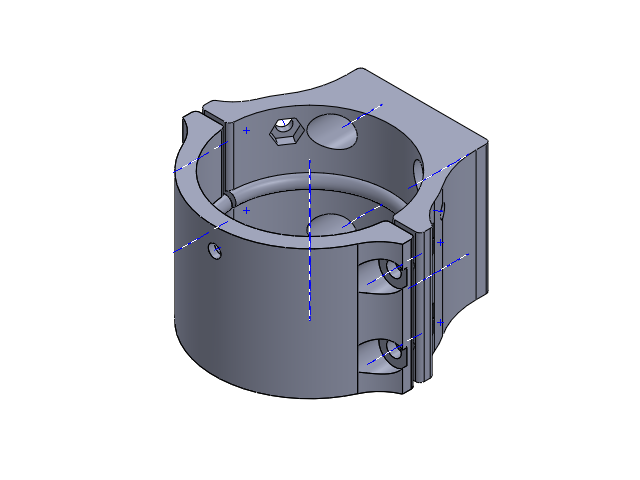
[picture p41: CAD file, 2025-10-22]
solidworks/support_pistolet_air_chaud/asm_support_reglable_v2.SLDASM
support_2parties_partFixed_v2
support_2parties_partAdd_v2

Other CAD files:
solidworks/Support_plaque_IR/asm_pince_fermoire.SLDASM
solidworks/support_carte_asm_g/asm_bati_support.SLDASM
solidworks/Support_plaque_IR/asm_support_plaqueIR_v4s.SLDASM
solidworks/Support_plaque_IR/asm_pince_fermoire_v2.SLDASM
solidworks/support_pistolet_air_chaud/asm_support_reglable.SLDASM
solidworks/Support_plaque_IR/asm_support_plaqueIR_v2.SLDASM
solidworks/Support_plaque_IR/ecrou_m3.SLDPRT
solidworks/Support_plaque_IR/entretoise_m3_20.SLDPRT
solidworks/Support_plaque_IR/fermoire_pince.SLDPRT
solidworks/Support_plaque_IR/mep_support_plaqueIR.SLDDRW
solidworks/Support_plaque_IR/pince.SLDPRT
solidworks/Support_plaque_IR/pince_v2.SLDPRT
solidworks/Support_plaque_IR/plaque_IR.SLDPRT
solidworks/Support_plaque_IR/plaquette_dent_de_scie.SLDPRT
solidworks/Support_plaque_IR/plaquette_serrage.SLDPRT
solidworks/Support_plaque_IR/plaquette_substitution.SLDPRT
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

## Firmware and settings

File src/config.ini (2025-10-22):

[DEFAULT]
portimprimante = COM7
portarduino = COM5
baudrate = 115200
pin_findecourse = 7
pin_buzzer = 2
pin_relaicyclechauffe = 4

[Constante]
vitesse_deplacement = 3000
pos_x_min_depose_ec = 96
pos_x_max_depose_ec = 229
espacement_ec_depose_x = 19
pos_y_min_depose_ec = 35
pos_y_max_depose_ec = 38.8
espacement_ec_depose_y = 0.4
hauteur_secu_z = 35
delta_z_posdesassemblage = 4

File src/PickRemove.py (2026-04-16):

import serial
import time
import tkinter as tk
from tkinter import messagebox
from tkinter import filedialog
import openpyxl
import pandas as pd
import configparser
import pyfirmata

#L'imprimante stocke les ordres et les exécute au fur et à mesure. Ainsi, afin de synchroniser
#l'envoi d'ordre et leur synchronisation, il est nécessaire d'attendre la fin du mouvement de 
#l'imprimante pour envoyer le prochain ordre.
def attendre_fin_mouvement():
    command='M400 \n'
    ser.write(command.encode())
    #print(f">> {command.strip()}")
    while True:
        line = ser.readline().decode().strip()
        #print(f">> {line}")
        if "ok" in line.lower():
            break

#Lorsque nous en sommes à l'étape du désassemblage, en plus d'attendre la fin du mouvement de l'imprimante,
# nous souhaitons également mesurer le temps écoulé entre le début de la descente du pistolet depuis la hauteur de sécu
# et le moment où ce dernier vient au contact avec un EC libérant le capteur de fin de course. Ainsi, le temps est mesuré
# entre l'envoi de la commande de descente du pistolet et le moment où le capteur de fin de course devient libre.
def attendre_fin_mouv_recup_ec():
    command='M400 \n'
    ser.write(command.encode())
    #print(f">> {command.strip()}")
    end=0
    try:
        while end==0:
            line = ser.readline().decode().strip()
            print(f">> {line}")
            value = endstop_pin.read()  # Renvoie True, False ou None
            if value is False:
                print("Capteur LIBRE (non pressé)")
                end=1
                return time.time()
            else:
                print("En attente du signal...")
                time.sleep(0.2)
    except KeyboardInterrupt:
        print("Fin du programme.")
        board.exit()

#La fonction "envoi_commande" permet d'envoyer un ordre à l'imprimante, puis d'attendre que cette dernière ait fini son mouvement.
#Dans certain cas il est nécessaire d'attendre deux fois la fin du mouvement pour ne pas perdre la synchronisation 
def envoi_commande(commande,opt):
    command=commande+' \n'
    ser.write(command.encode())
    #print(f">> {command.strip()}")
    time.sleep(1)  # Pause entre les commandes (ajustable)
    
    
    # Lecture de la réponse éventuelle de l'imprimante
    while True:
        response = ser.readline().decode().strip()
        # if response:
        #     print(f"<< boucle1 {response}")
        if "ok" in response.lower():
            if "G28" in commande:
                attendre_fin_mouvement()
                time.sleep(0.5)
                break
            elif opt==0:
                return attendre_fin_mouv_recup_ec()
                time.sleep(0.5)
                break
            else:
                attendre_fin_mouvement()
                time.sleep(0.5)
                attendre_fin_mouvement()
                time.sleep(0.5)
                break
            
#Cette fonction permet de retourner la position de l'imprimante. Néanmoins, cette position 
#n'est pas la position réelle, mais plutôt la future position de cette dernière une fois le mouvement accompli.
def pos_actuel():
    command='M114 \n'
    ser.write(command.encode())
    print(f">> {command.strip()}")
    time.sleep(0.5)  # Pause entre les commandes (ajustable)
    while True:
        line = ser.readline().decode().strip()
        print(f">> {line}")
        if "x:" in line.lower():
            coords = [0, 0, 0]
            i=0
            
            # Ne garder que la partie avant "Count"
            part = line.split("E")[0].strip()
            print(part)
            trash, part = part.split('X:')
            coords[0], part = part.split('Y:')
            coords[1], coords[2] = part.split('Z:')
            return coords
            break

# Cette fonction permet de générer une fenêtre pop-up avec le message transmis en entrée.        
def popUp_information(message):
    win = tk.Tk()
    win.title("Information")
    win.attributes('-topmost', True)
    win.geometry("450x150")
    
    tk.Label(win, text=message, pady=10).pack()
    tk.Button(win, text="OK", command=win.destroy).pack()
    
    win.mainloop()

#Cette fonction permet la récupération du fichier Excel permettant la récupération des composants.
# Elle permet la génération d'une fenêtre pop-upp ainsi qu'une fenêtre de sélection du fichier cible
def open_file():
    popUp_information("Veuillez sélectionner le fichier excel organisé comme suis:\n"
                      "Nom composant     Position X     Position Y\n"
                      "R1                         12.5                 24.8\n"
                      "C3                         45.0                 10.2\n"
                      "U1                         30.0                 35.0\n"
                      "(avec la case Nom composant correspondant à la cellule excel A1)")
    file_path = filedialog.askopenfilename(title="Ouvrir un fichier", filetypes=[("Fichiers excel", "*.xls")])
    print(file_path)
    try:
        df = pd.read_excel(file_path)

    except FileNotFoundError:
        print(f"Fichier non trouvé : {file_path}")
    except Exception as e:
        print(f"Erreur lors de la lecture du fichier : {e}")
    return df, file_path

# Cette fonction permet d'extraire les données du fichier de configuration
def recup_donnee_config():
    config = configparser.ConfigParser()
    try:
        config.read('config.ini')
        default = config['DEFAULT']
        constante = config['Constante']
        portImprimante=default['portImprimante']
        portArduino=default['portArduino']
        baudrate=default['baudrate']
        pin_finDeCourse=default['pin_finDeCourse']
        pin_buzzer=default['pin_buzzer']
        pin_relaiCycleChauffe=default['pin_relaiCycleChauffe']
        pos_x_min_depose_ec=float(constante['pos_x_min_depose_ec'])
        pos_x_max_depose_ec=float(constante['pos_x_max_depose_ec'])
        espacement_ec_depose_x = float(constante['espacement_ec_depose_x'])
        pos_y_min_depose_ec=float(constante['pos_y_min_depose_ec'])
        pos_y_max_depose_ec=float(constante['pos_y_max_depose_ec'])
        espacement_ec_depose_y = float(constante['espacement_ec_depose_y'])
        vitesse_deplacement=int(constante['Vitesse_deplacement'])
        hauteur_secu_z=int(constante['hauteur_secu_z'])
        delta_z_posDesassemblage=int(constante['delta_z_posDesassemblage'])
    except FileNotFoundError:
        print(f"Fichier non trouvé : {config.ini}")
    except Exception as e:
        print(f"Erreur lors de la lecture du fichier : {e}")
    return portImprimante, portArduino,baudrate, pin_finDeCourse, pin_buzzer, pin_relaiCycleChauffe, pos_x_max_depose_ec, pos_x_min_depose_ec, espacement_ec_depose_x, pos_y_max_depose_ec, pos_y_min_depose_ec,espacement_ec_depose_y,vitesse_deplacement,hauteur_secu_z, delta_z_posDesassemblage
        
# Charger le fichier Excel
fichier_excel, file_path= open_file()
print ("Fichier excel récupéré")
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

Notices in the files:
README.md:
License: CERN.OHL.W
